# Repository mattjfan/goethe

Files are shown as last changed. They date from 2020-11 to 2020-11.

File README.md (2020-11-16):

# goethe
Accurate, low volume robotic color matching and mixing platform for medium to high viscosity paint

## What is this project?
The idea of this project is to create a physical version of the colorpicker/eyedropper or
palette creators you might see in a digital image-editing software like photoshop, but for paint
(and in theory other physical liquid mediums).

## What do we have so far?
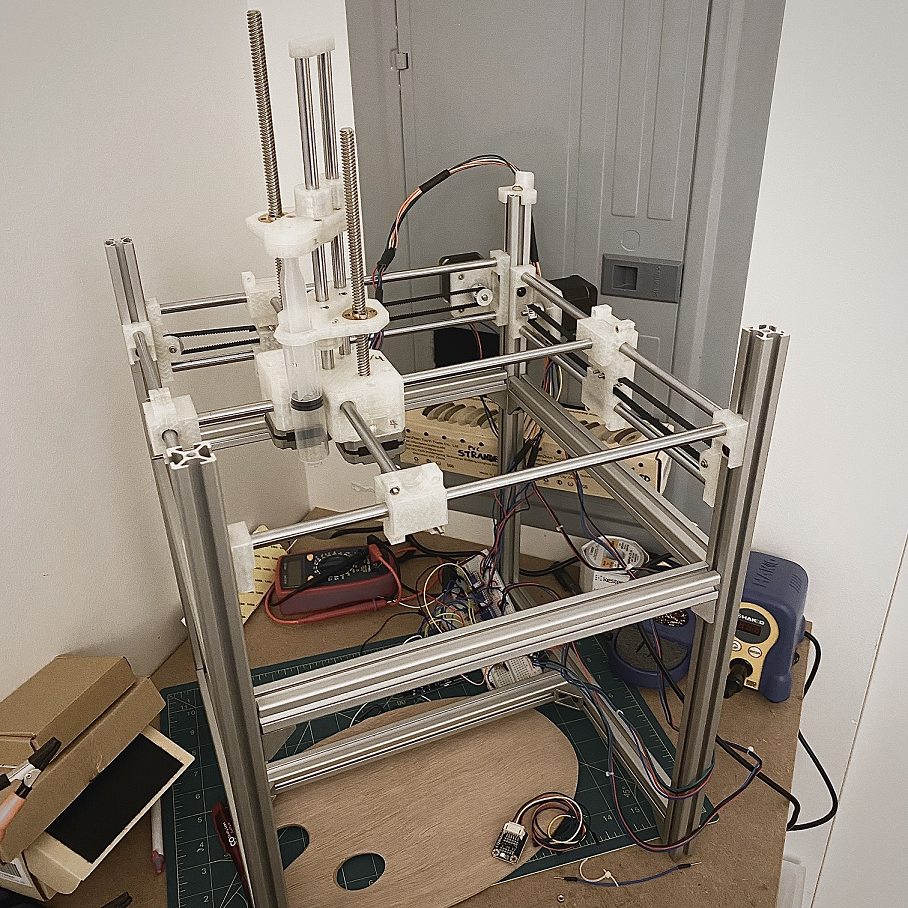
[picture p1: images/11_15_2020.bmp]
v1 prototype


A (grossly over-engineered, but still usable) prototype with XY-axis control, and a raisable and controllable syringe for picking up and putting down paints (and potentially stirring). Currently based on the Arduino UNO, will be moving to Arduino Mega soon for development, and considering out other AVR platforms for longer term after initial prototyping. The prototype has everything it needs for movement and controls, and has basic movement (non-control looped) for the carriage and the syringe already validated. Currently missing a platform to hold the paint and water reservoirs, and a sliding platform to hold the user's palette. Also not wired up for the color sensor yet, and I haven't made the CAD designs for the sensor pen/eyedropper (key thing here is that we want the tool to reject ambient light for color consistency across usage environments). A lot of the control code is written (but unvalidated), and is also pretty rough but usable. Actual wrappers for using the system for color mixing is still WIP.

*Important note: The repo right now is still just being used as a place for me to dump and track things as I continue development. As such, files may be disorganized or incorrectly labeled, code can be expected to still be buggy or unvalidated, and this repo may not contain all resources associated with the project, such as notes or a BOM for the non-3d-printed parts. You're free to try to build your own, but **be advised that some parts may be missing or unfinished**. If the results of this project turn out good, I'll go back through and do some housekeeping/updates later to make it easier to build your own.*

## Next Steps
Well, first I want to finish this prototype. Then, I want to mock a prototype that uses peristaltic pumps and a strain guage/scale as a 
potentially faster, cheaper, simpler design, and compare color accuracy and precision across the two designs. (This design was actually one of
the original concepts, although I rejected it bc I liked the elegance of the V1 design (only one extruder), and thought it may have issues with
accuracy. After seeing industrial paint mixing machines and that they work with a similar pump design, I figured it's worth revisiting (although it's
possible that the color accuracy of this design at low volume in contrast to paint can volume is just not very good). This design technically uses
more motors (and potentially even more if we want to add powered XY axis support for comparable workspace instead of static nozzle placement),
but the mixing process steps are likely simpler in this approach, and worth considering given the relatively cheap cost of peristaltic pumps.

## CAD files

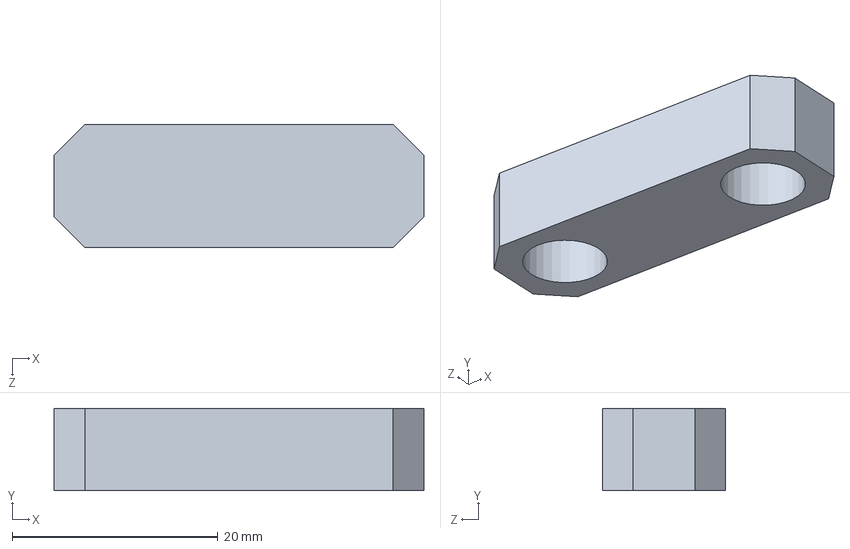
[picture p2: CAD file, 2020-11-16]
hardware/cad/dispenser/shaft_cap/shaft_cap_v1.SLDPRT
36.0 x 8.00 x 12.0 mm

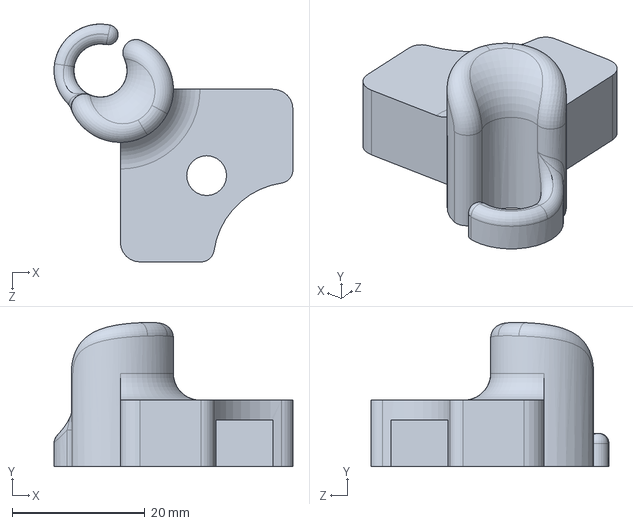
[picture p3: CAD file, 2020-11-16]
hardware/cad/extras/wire_guard/wire_guard.SLDPRT
36.0 x 21.7 x 35.8 mm

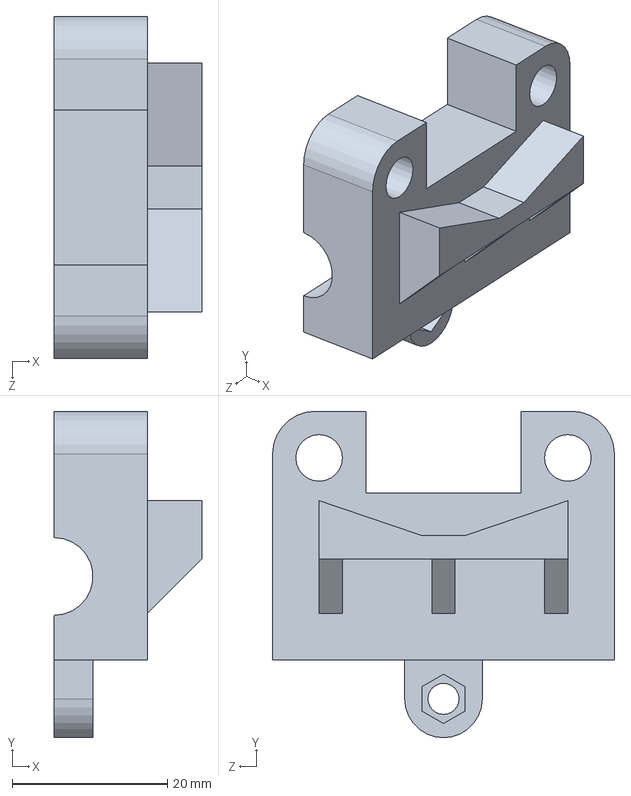
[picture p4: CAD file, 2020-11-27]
hardware/cad/gantry_v2/single_rod_slider_inside.SLDPRT
19.0 x 42.0 x 44.0 mm

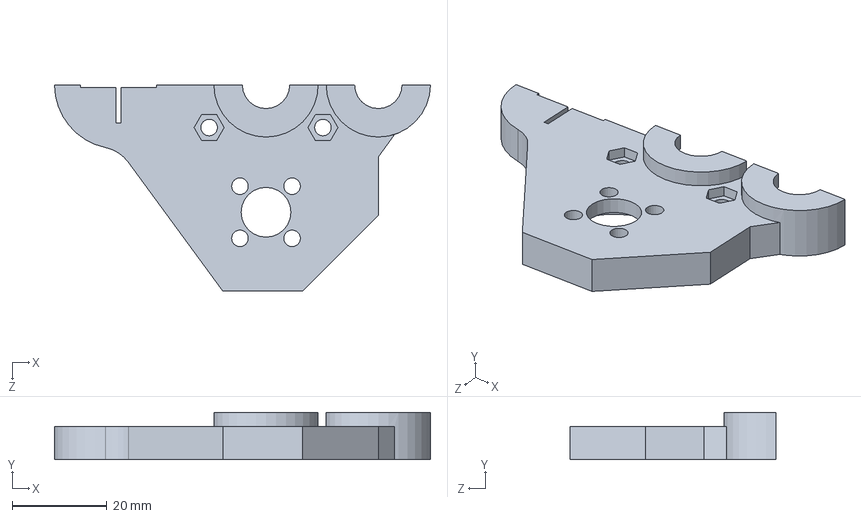
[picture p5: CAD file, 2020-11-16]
hardware/cad/plunger_plate/plunger_plate_hemi_L_v2.SLDPRT
79.3 x 10.0 x 43.5 mm

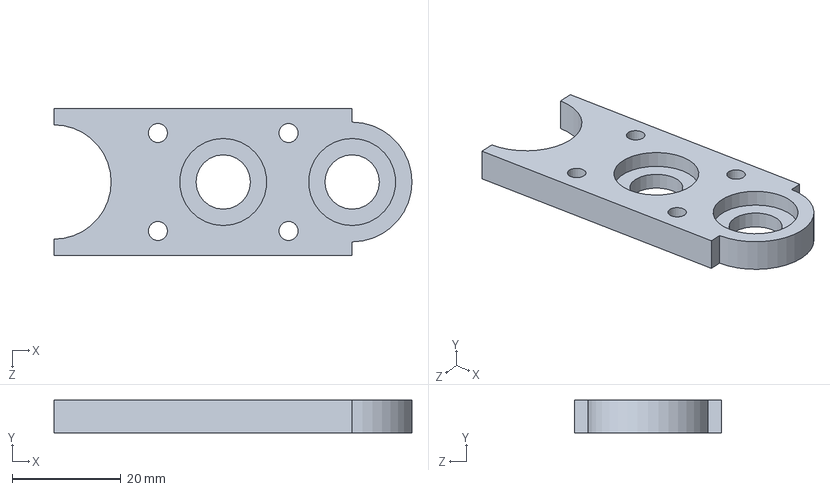
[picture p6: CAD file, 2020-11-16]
hardware/cad/syringe_plate/syringe_plate_cap_v1.SLDPRT
65.8 x 6.00 x 27.0 mm

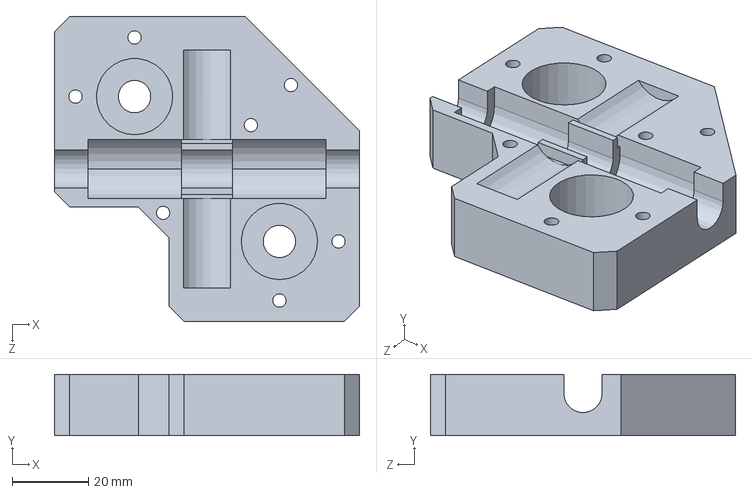
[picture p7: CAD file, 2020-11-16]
hardware/cad/dispenser/motor_plate/motor_plate_top_v4.SLDPRT
80.0 x 16.0 x 80.0 mm

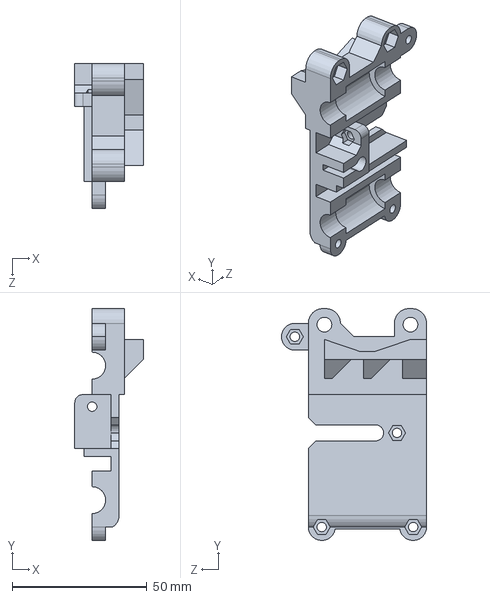
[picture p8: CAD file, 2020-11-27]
hardware/cad/gantry_v2/double_rod_slider_inside_v2.SLDPRT
25.5 x 86.2 x 54.0 mm

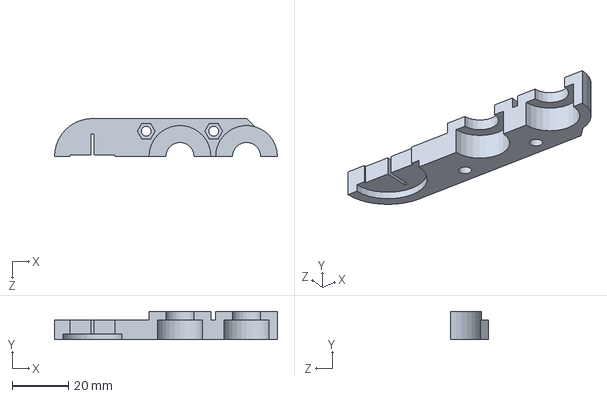
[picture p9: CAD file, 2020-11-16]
hardware/cad/plunger_plate/plunger_plate_hemi_S_v2.SLDPRT
79.3 x 10.0 x 13.5 mm

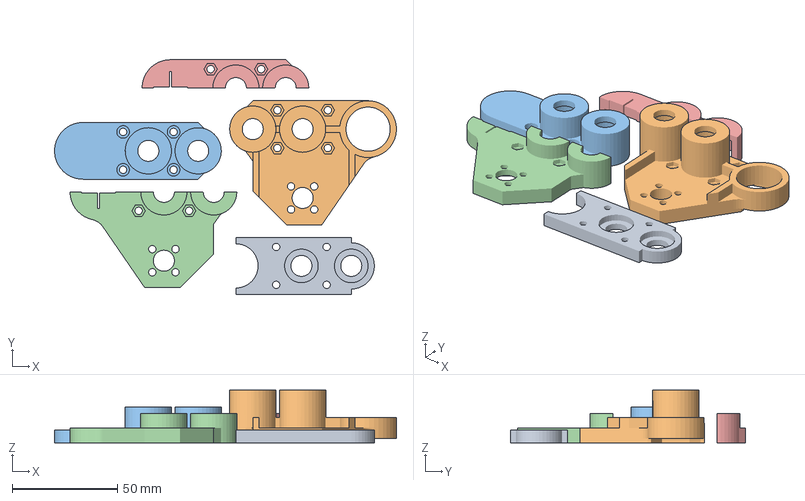
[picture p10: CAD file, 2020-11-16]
hardware/cad/syringe_plate/syringe_and_extruder_plates_v1.3mf
162.5 x 111.5 x 25.0 mm
syringe_plate_cap_v1.STL
syringe_plate_v1.STL
plunger_plate_cap_v1.STL
plunger_plate_hemi_L_v1.STL
plunger_plate_hemi_S_v1.STL

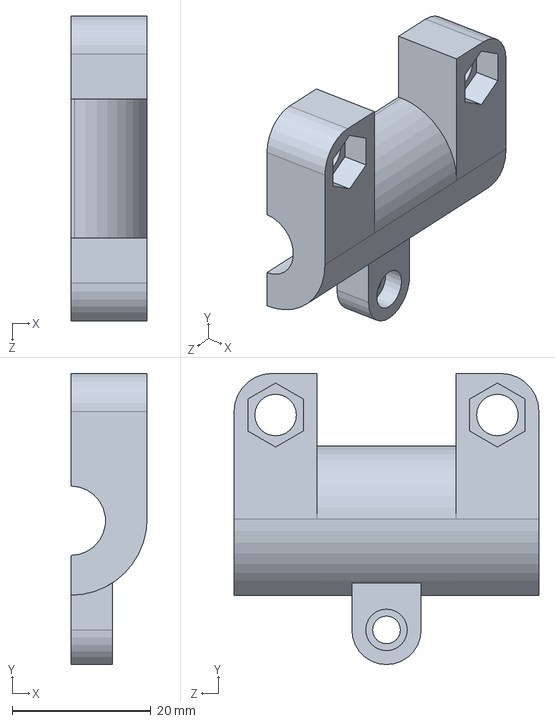
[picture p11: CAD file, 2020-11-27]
hardware/cad/gantry_v2/single_rod_slider_outside.SLDPRT
11.0 x 42.0 x 44.0 mm

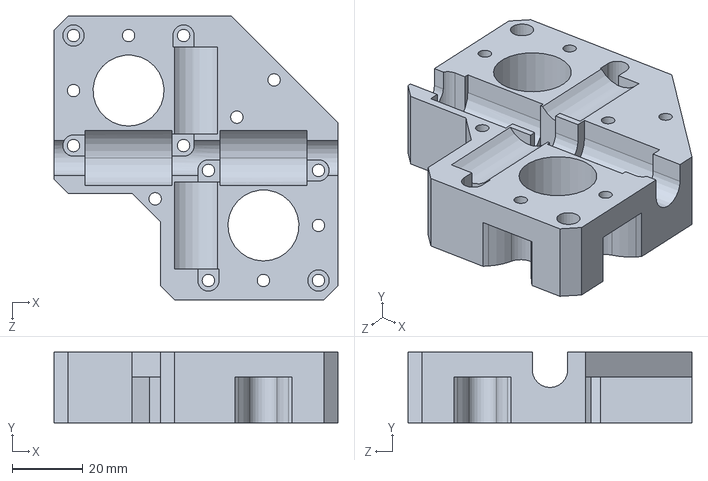
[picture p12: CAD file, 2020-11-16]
hardware/cad/dispenser/motor_plate/motor_plate_v4.SLDPRT
80.0 x 20.0 x 80.0 mm

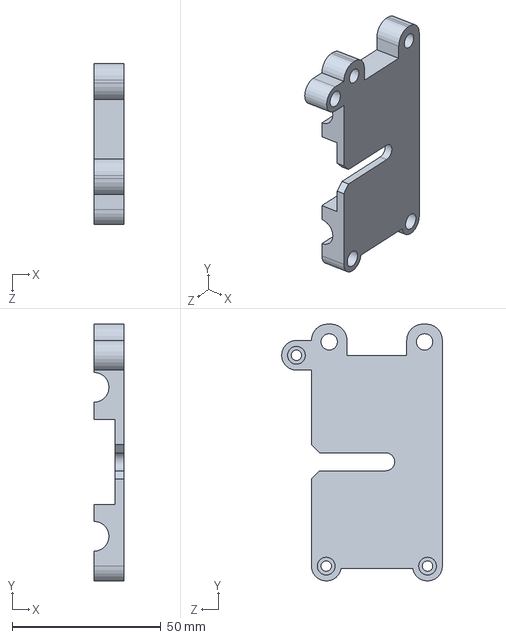
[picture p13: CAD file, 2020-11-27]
hardware/cad/gantry_v2/double_rod_slider_outside_v2.SLDPRT
10.0 x 86.2 x 54.0 mm

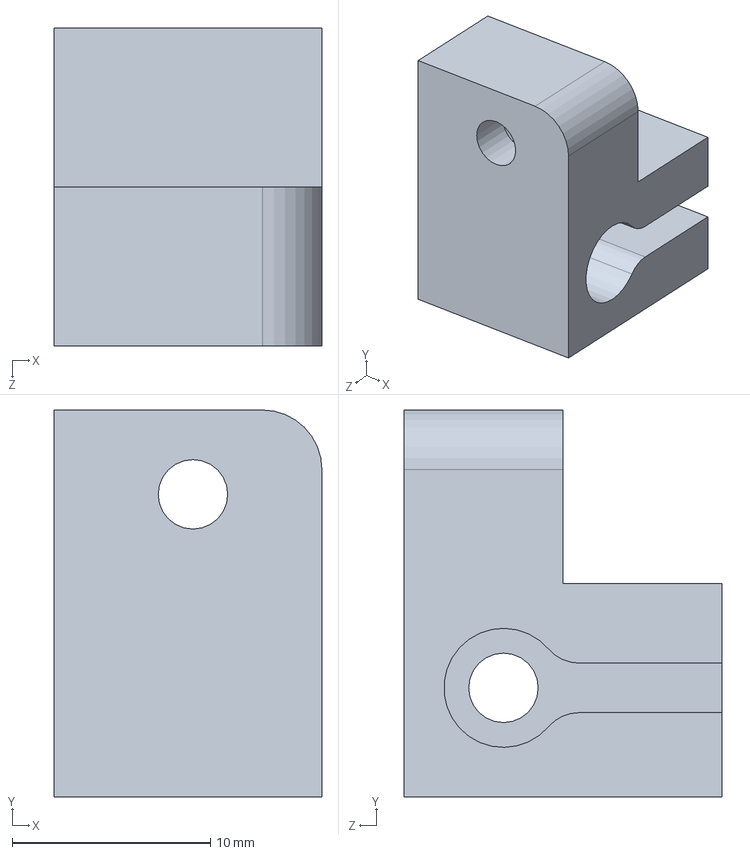
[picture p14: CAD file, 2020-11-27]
hardware/cad/gantry_v2/double_rod_slider_tensioner_v2.SLDPRT
13.5 x 19.5 x 16.0 mm

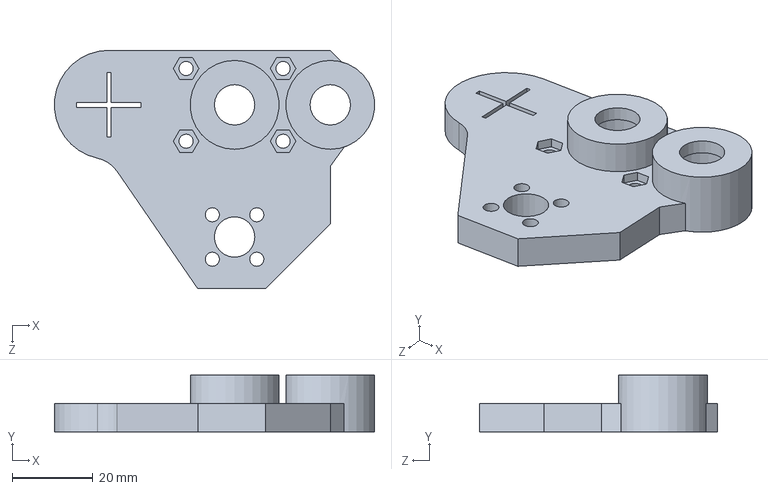
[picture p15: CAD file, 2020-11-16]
hardware/cad/plunger_plate/plunger_plate_v1.SLDPRT
79.2 x 14.0 x 59.0 mm

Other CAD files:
hardware/cad/syringe_plate/syringe_plate_v3.SLDPRT
hardware/cad/gantry_v2/single_rod_slider_outside_v2.SLDPRT
hardware/cad/gantry_v2/single_rod_slider_inside_v2.SLDPRT
hardware/cad/plunger_plate/plunger_plate_cap_v2.SLDPRT
hardware/cad/dispenser/motor_plate/motor_plate_top_v3.SLDPRT
hardware/cad/dispenser/motor_plate/motor_plate_top_v3.STL
hardware/cad/dispenser/motor_plate/motor_plate_top_v4.STL
hardware/cad/dispenser/motor_plate/motor_plate_v1.SLDPRT
hardware/cad/dispenser/motor_plate/motor_plate_v2.SLDPRT
hardware/cad/dispenser/motor_plate/motor_plate_v3.SLDPRT
hardware/cad/dispenser/motor_plate/motor_plate_v3.STL
hardware/cad/dispenser/motor_plate/motor_plate_v4.STL
hardware/cad/dispenser/shaft_cap/shaft_cap_v1.STL
hardware/cad/extras/wire_guard/wire_guard.STL
hardware/cad/gantry/double_rod_holder/double_rod_holder_v1.STL
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

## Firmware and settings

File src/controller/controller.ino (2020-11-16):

//#include "controller.h"
#include <EEPROM.h>
#include <TMCStepper.h>

#define LOC_RED (Point) {7, 13}
#define LOC_BLUE (Point) {0,0}
#define LOC_YELLOW (Point) {0,0}
#define LOC_BLACK (Point) {0,0}
#define LOC_WHITE (Point) {0,0}
#define LOC_DILUTE (Point) {0,0}
#define LOC_CLEAN (Point) {0,0}
#define HEIGHT_CALIBRATE 0 // Height for stall calibration, and lowest possible height. Should generally be 0
#define HEIGHT_LOAD HEIGHT_CALIBRATE
#define HEIGHT_MOVE 10 // Height for moving around. Should be tall enough to clear all obstacles, prob. want this to be your largest height
#define PLUNGER_MAX_HEIGHT 100 // Max height of plunger.
#define PLUNGER_DIAMETER 20
#define HEIGHT_DISPENSE HEIGHT_MOVE
#define HEIGHT_DISPENSE_WATER HEIGHT_DISPENSE // if you want to specify a water dispense height to minimize splashing
#define BB_DISPENSE_L (Point) {50,50} // closest to origin corner for dispensing bounding box
#define BB_DISPENSE_U (Point) (100,100} // farthest from origin corner for dispensing bounding box
#define CW HIGH
#define CCW LOW

#define STEPS_PER_REV (double) 200
#define MICROSTEPS (double) 8
#define DRIVE_PULLEY_RADIUS (double) 6.1 // in mm
#define DRIVE_SCREW_PITCH (double) 8.0 // in mm

#define STEP_DIST_SYRINGE ( DRIVE_SCREW_PITCH / ( STEPS_PER_REV * MICROSTEPS ))
#define STEP_DIST_X ( (2 * PI * DRIVE_PULLEY_RADIUS) / ( STEPS_PER_REV * MICROSTEPS ))
#define STEP_DIST_Y STEP_DIST_X

#define STALL_PIN_SYRINGE A0
#define STALL_PIN_PLUNGER A1
#define STALL_PIN_X A2
#define STALL_PIN_Y A3

#define MOTOR_SYRINGE StepperMotor(4, 5, STALL_PIN_SYRINGE, 3, STEP_DIST_SYRINGE, 140, CW) // defining motor wholesale as macro instead of individual pins
#define MOTOR_PLUNGER StepperMotor(6, 7, STALL_PIN_PLUNGER, 3, STEP_DIST_SYRINGE, 90, CW)
#define MOTOR_X StepperMotor(8, 9, STALL_PIN_X, A4, STEP_DIST_X, 280, CW)
#define MOTOR_Y StepperMotor(10, 11, STALL_PIN_Y, A5, STEP_DIST_Y, 280, CCW)

#define CONFIG_RX 12
#define CONFIG_TX 13
#define STALL_VALUE 40
#define DRIVER_ADDRESS 0b00 // TMC2209 Driver address according to MS1 and MS2

#define R_SENSE 0.11f // Match to your driver
                      // SilentStepStick series use 0.11
                      // UltiMachine Einsy and Archim2 boards use 0.2
                      // Panucatt BSD2660 uses 0.1
                      // Watterott TMC5160 uses 0.075

TMC2209Stepper driver(CONFIG_RX, CONFIG_TX, R_SENSE, DRIVER_ADDRESS);

using namespace TMC2208_n;

class StepperMotor {
  public:
//    StepperMotor(int step_pin, int dir_pin, int stall_pin = -1, int enable_pin = -1, double mm_per_step = 0, int step_delay = 1) {
//      this->step_pin = step_pin;
//      this->dir_pin = dir_pin;
//      this->stall_pin = stall_pin;
//      this->enable_pin = enable_pin;
//      this->step_delay = step_delay;
//      this->mm_per_step = mm_per_step;
//      pinMode(step_pin, OUTPUT);
//      pinMode(dir_pin, OUTPUT);
//      if (stall_pin >= 0) {
//        this->stall_pin = stall_pin;
//        pinMode(stall_pin, INPUT);
//      }
//      if (enable_pin >= 0) {
//        this->enable_pin = enable_pin;
//        pinMode(enable_pin, OUTPUT);
//        digitalWrite(enable_pin, LOW);
//      }
//    }
//    StepperMotor( int step_pin, int dir_pin, double mm_per_step, int step_delay = 1) {
//    }
//    StepperMotor( int step_pin, int dir_pin, int stall_pin, double mm_per_step, int step_delay = 1) {
//     
//    }
    StepperMotor( int step_pin, int dir_pin, int stall_pin, int enable_pin, double mm_per_step, double max_pos, double increasing_direction = CW, int step_delay = 1) {
      this->step_pin = step_pin;
      this->dir_pin = dir_pin;
      this->stall_pin = stall_pin;
      this->enable_pin = enable_pin;
      this->mm_per_step = mm_per_step;
      this->step_delay = step_delay;
      this->max_pos = max_pos;
      this->inc_dir = increasing_direction;
      pinMode(step_pin, OUTPUT);
      pinMode(dir_pin, OUTPUT);
      pinMode(stall_pin, INPUT); // included with next gen design in mind. Currently not used internally, stall refs currently managed in global scope
      pinMode(enable_pin, INPUT);
    }
    void step_dist_cw(double dist, int step_delay = 1) {
      step_cw((int) dist / mm_per_step, step_delay);
    }
    void go_up(double dist) {
      double target_pos = pos + dist;
      if (target_pos > max_pos) {
        target_pos = max_pos;
      }
      digitalWrite(step_pin, LOW);
      digitalWrite(dir_pin, inc_dir);
      while (pos < target_pos) {
        digitalWrite(step_pin, HIGH);
        delayMicroseconds(step_delay);
        digitalWrite(step_pin, LOW);
        pos += mm_per_step;
      }
    }

    void go_down(double dist) {
      double target_pos = pos - dist;
      if (target_pos < 0) {
        target_pos = 0;
      }
      digitalWrite(step_pin, LOW);
      digitalWrite(dir_pin, !inc_dir);
      while (pos > target_pos) {
        digitalWrite(step_pin, HIGH);
        delayMicroseconds(step_delay);
        digitalWrite(step_pin, LOW);
        pos -= mm_per_step;
      }
    }

    void go_to_position(double target_position) {
//      Serial.println("Goin to tha position");
      if (target_position > max_pos) {
        return;
      }
      digitalWrite(step_pin, LOW);
      if (pos < target_position) {
        digitalWrite(dir_pin, inc_dir);
        while (pos < target_position) {
          digitalWrite(step_pin, HIGH);
          delayMicroseconds(step_delay);
          digitalWrite(step_pin, LOW);
          pos += mm_per_step;
        }
      } else if (pos > target_position) {
        digitalWrite(dir_pin, !inc_dir);
        while (pos > target_position) {
          digitalWrite(step_pin, HIGH);
          delayMicroseconds(step_delay);
          digitalWrite(step_pin, LOW);
          pos -= mm_per_step;
        }
      } 
    }
    void step_cw(int num_steps, int step_delay = 1) {
      step_(num_steps, CW, step_delay);
    }

    void step_ccw(int num_steps, int step_delay = 1) {
      step_(num_steps, CCW, step_delay);
    }

    void step(int dir, int delay_micros = 20) {
      digitalWrite(dir_pin, dir);
      digitalWrite(step_pin, HIGH);
      delayMicroseconds(delay_micros);
      digitalWrite(step_pin, LOW);
    }
    void calibrate() {
      digitalWrite(dir_pin, !inc_dir);
      digitalWrite(step_pin, LOW);
//      while(1) {
      for (int i = 0; i <= round(max_pos / mm_per_step); i++) { // times out if stall isn't triggered 
        if (isStalled()) {
          break;
        }
        digitalWrite(step_pin, HIGH);
        delay(step_delay);
        digitalWrite(step_pin, LOW);
      }
      pos = 0;
    }
    void calibrate_reverse() { // calibrate to max_pos instead of zero
      digitalWrite(dir_pin, inc_dir);
      digitalWrite(step_pin, LOW);
      for (int i = 0; i <= round(max_pos / mm_per_step); i++) { // times out if stall isn't triggered 
        if (isStalled()) {
          break;
        }
        digitalWrite(step_pin, HIGH);
        delay(step_delay);
        digitalWrite(step_pin, LOW);
      }
      pos = max_pos;
    }
//    void calibrate(int dir, int step_delay = -1) { // TODO: may want to add a max timeout option
//      digitalWrite(dir_pin, dir);
//      if (step_delay < 0) {
//        step_delay = this->step_delay;
//      }
//      while(1) {
//        if (isStalled()) {
//          break;
//        }
//        digitalWrite(step_pin, HIGH);
//        delay(step_delay);
//        digitalWrite(step_pin, LOW);
//      }
//      // clean-up so motor can be used again.
//      reset();
//    }
    void setStalled(bool isStalled) { // kludge so that global interrupt handlers can set this value
      stalled = isStalled;
    }
    bool isStalled() {
      return stalled;
//      if (stall_pin >= 0 &&
//        digitalRead(stall_pin) == HIGH) {
//         Serial.println("Fuck, we stalled");
//        return true;
//      }
//      return false;
    }

    void reset() {
      this->disable();
      delay(this->reset_delay);
      this->enable();
      this->stalled = false;
    }

    void enable() {
      digitalWrite(enable_pin, LOW);
    }
    
    void disable() {
      digitalWrite(enable_pin, HIGH);
    }
    
  private:
    int step_pin;
    int dir_pin;
    int stall_pin;
    int enable_pin;
    int step_delay;
    double mm_per_step;
    int inc_dir = CW;
    double pos = 0;
    double max_pos;
    int reset_delay = 20;
    bool stalled = false;
    void interrupt_handler () {
      stalled = true;
    }
    void step_(int num_steps, int dir, int step_delay = -1) {
      if (step_delay < 0) {
        step_delay = this->step_delay; // reset local reference
        // I think this is mem safe bc step_delay should be passed by value
      }
      digitalWrite(dir_pin, dir);
      for (int i = 0; i < num_steps; i++) {
        digitalWrite(step_pin, HIGH);
        delay(step_delay);
//        delayMicroseconds(100);
        digitalWrite(step_pin, LOW);
        if (isStalled()) {
          reset();
          break;
        }
      }
    }
};

//class GantryAxis {
//  public:
//    GantryAxis(StepperMotor motor) {
//    }
//}

class Syringe {
  public:
    Syringe(StepperMotor body, StepperMotor plunger, double diameter = 10.0, double step_distance = 0.1, int step_delay = 1){
      *(this->body_ptr) = body;
      *(this->plunger_ptr) = plunger;
      this->step_distance = step_distance;
      this->UP_DIR = CW;
      this->diameter = diameter;
      this->step_distance = step_distance;
      this->step_delay = step_delay;
    }
    void moveTo(float target_height){ // TODO: check that it moves within height bounds
      if (target_height > syringe_height) {
        while(target_height > syringe_height) {
          body.step(UP_DIR); // technically not truly synchronous...
          plunger.step(UP_DIR);
          delay(step_delay);
          syringe_height += step_distance;
        }
      } else {
        while(target_height < syringe_height) {
          body.step(!UP_DIR);
          plunger.step(!UP_DIR);
          delay(step_delay);
          syringe_height -= step_distance;
        }
      }
    }
    void load(double volume) { // volume in mm^3
      double target_height = plunger_height + heightFromVolume(volume); // v = PI * d^2 * h / 4
      while(plunger_height < target_height){
        plunger.step(UP_DIR);
        delay(step_delay);
        plunger_height += step_distance;
      }
    }
    void dispense(double volume) {
      double target_height = plunger_height - heightFromVolume(volume);
      while (plunger_height > target_height) {
        plunger.step(!UP_DIR);
        delay(step_delay);
        plunger_height -= step_distance;
      }
    }
  private:
    double heightFromVolume(double volume) {
      return (4.0 * volume) / (PI * diameter * diameter);
    }
    StepperMotor &body = *body_ptr; // kludge to reference by name
                              // should probably refactor at some point to
                              // declare with .h/.hpp and use an initializer list
    StepperMotor &plunger = *plunger_ptr;
    
    
    StepperMotor* body_ptr = nullptr;
    StepperMotor* plunger_ptr = nullptr;
    int UP_DIR;
    double syringe_height = 0.0;
    double plunger_height = 0.0;
    double step_distance;
    double diameter;
    int step_delay;
};

class Gantry {
  public:
    Gantry(double step_distance = 0.1){
      
    }
  private:
    double x, y;
};

typedef struct Point {
  int x;
  int y;
} Point;

class Color {
  public:
    Color(double r, double b, double y, double w, double k) {
      // basic color w/ no water dilution
      double sum = r + b + y + w + k;
      this->r_ = r /= sum;
      this->b_ = b /= sum;
      this->y_ = y /= sum;
      this->w_ = w /= sum;
      this->k_ = k /= sum;
      this->c_ = 0.0;
    }
    
    Color(double r, double b, double y, double w, double k, double c) {
      // allow for specifying water % for diluted / wet mixes
      double sum = r + b + y + w + k + c;
      this->r_ = r /= sum;
      this->b_ = b /= sum;
      this->y_ = y /= sum;
      this->w_ = w /= sum;
      this->k_ = k /= sum;
      this->c_ = c /= sum;
    }
    
    const double &r = r_;
    const double &b = b_;
    const double &y = y_;
    const double &w = w_;
    const double &k = k_;
    const double &c = c_;
  private:
    double r_;
    double b_;
    double y_;
    double w_;
    double k_;
    double c_;
};

void configure_stallguard() {
  driver.beginSerial(19200);
  driver.begin();
  driver.toff(4);
  driver.blank_time(24);
  driver.rms_current(400); // mA
  driver.microsteps(MICROSTEPS); // was originally set at 16
  driver.TCOOLTHRS(0xFFFFF); // 20bit max
  driver.semin(5);
  driver.semax(2);
  driver.sedn(0b01);
  driver.SGTHRS(STALL_VALUE);
}
/**
 * Basic motor tests checking for movement
 */
void motor_test_basic(int steps = 1500, int period = 3){
  // testing syringe motor
  if(Serial) {
    Serial.print("Testing syringe...");
  }
  MOTOR_SYRINGE.reset();
  MOTOR_SYRINGE.step_cw(steps, period);
  MOTOR_SYRINGE.step_ccw(steps, period);
  if (Serial) {
    Serial.println("done.");
  }
  // testing plunger motor
  if(Serial) {
    Serial.print("Testing plunger...");
  }
  MOTOR_PLUNGER.reset();
  MOTOR_PLUNGER.step_cw(steps, period);
  MOTOR_PLUNGER.step_ccw(steps, period);
  if (Serial) {
    Serial.println("done.");
  }
  // testing x carriage motor
  if(Serial) {
    Serial.print("Testing X carriage...");
  }
  MOTOR_X.reset();
  MOTOR_X.step_cw(steps, period);
  MOTOR_X.step_ccw(steps, period);
  if (Serial) {
    Serial.println("done.");
  }
  // testing y carriage motor
  if(Serial) {
    Serial.print("Testing Y carriage...");
  }
  MOTOR_Y.reset();
  MOTOR_Y.step_cw(steps, period);
  MOTOR_Y.step_ccw(steps, period);
  if (Serial) {
    Serial.println("done.");
  }
}

// callback for computer serial command interface
bool queue_events = false; // should events be queued
bool serial_blocked = false; // global flag to let us know if we should throw stuff away
void serialEvent() {
  String s = Serial.readStringUntil('\n');
  if (serial_blocked && !queue_events) { // throw away events received while you were running old event
    // unless you have queueing of events turned on.
    Serial.println("Ignoring message " + s); // Say that event is being thrown away
  } else { // main logic block goes here
      serial_blocked = true;
      serialCallback(s);
  }
  if (!Serial.available()) { // Unblocking new events if we've processed all stale events
      serial_blocked = false;
  }
}

void serialCallback(String msg) {
  String command = "";
  String payload = "";
  int argc = 1;
  String str = "";
  bool isCommand = true;
  for (char const &c: msg) {
    if (isCommand) {    
      if (c != ' ') {
        command += c;
      } else {
        isCommand = false;
      }
    } else {
      payload += c;
    }
  }
  if (command == "calibrate") {
    if (payload == "x") {
      Serial.print("Calibrating X-axis...");
      MOTOR_X.calibrate();
      Serial.println("done.");
    } else {
      Serial.println("Unrecognized argument " + payload + " for command " + command);
    }
  } else if (command == "movex") {
    double pos = payload.toDouble();
    if (pos || payload == "0" || payload == "0.0") {
      Serial.println(pos);
      MOTOR_X.go_to_position(pos);
      Serial.println("At requested position");
      
    } else {
      Serial.println("Unrecognized argument " + payload + " for command " + command);
    }
  } else {
    Serial.println("Unrecognized command " + command);
  }

//  if (msg == "calibrate x") {
//    // do calibration
//  } else if ( msg
//      Serial.println("Hello " + msg);
//      delay(5000);
//      Serial.println("Goodbye " + msg);
}

void syringe_interrupt_handler() {
  MOTOR_SYRINGE.setStalled(true);
}

void plunger_interrupt_handler() {
  MOTOR_PLUNGER.setStalled(true);
}

void x_interrupt_handler() {
  MOTOR_X.setStalled(true);
}

void y_interrupt_handler() {
  MOTOR_Y.setStalled(true);
}



void setup() {
  // put your setup code here, to run once:
  configure_stallguard();
  Serial.begin(9600);
  while(!Serial){}
  Serial.println("Starting");
  // Below is kludge to hook up motor stall pins to interrupts
  // ideally this could be handled in the class directly, but the instance method prototypes can't be used directly with attachInterrupt
  // and I can't use non-standard C++ libraries in AVR w/o adding extra bulk
  // Could theoretically also do live polling in the main loop, but would then have to wrangle all of our tasks into short-lived enough to be viable
  // in that approach... 
  // This current approach is messy, and strews the innards of our motor abstraction all over the place (and also exposes internal state for stall setting)
  // but it *should* at least work for now without needing to add extra stuff to AVR deps
  // May revisit this later, and end up adding the extra dependencies for a less fubar approach
  pinMode(STALL_PIN_SYRINGE, INPUT);
  pinMode(STALL_PIN_PLUNGER, INPUT);
  pinMode(STALL_PIN_X, INPUT);
  pinMode(STALL_PIN_Y, INPUT);
  attachInterrupt(digitalPinToInterrupt(STALL_PIN_SYRINGE), syringe_interrupt_handler, RISING);
  attachInterrupt(digitalPinToInterrupt(STALL_PIN_PLUNGER), plunger_interrupt_handler, RISING);
  attachInterrupt(digitalPinToInterrupt(STALL_PIN_X), x_interrupt_handler, RISING);
  attachInterrupt(digitalPinToInterrupt(STALL_PIN_Y), y_interrupt_handler, RISING);
//  readStringUntil(
//  configure_stallguard();
//  motor_test_basic(2400,1);
//  Serial.println("Finishing");
  
//  Serial.begin(9600);
//  Serial.print("What up hello!\n");
//  Serial.print("Red x: ");
//  Serial.print(LOC_RED.x);
//  Serial.print(", y: ");
//  Serial.print(LOC_RED.y);
//  Serial.print("\n");
//  Serial.print("Dispensing height: ");
//  Serial.print(HEIGHT_DISPENSE);
//  delay(2000);
//  Serial.println("");
//  Serial.println("Starting: ");
//  MOTOR_SYRINGE.reset();
//  MOTOR_SYRINGE.step_cw(5000, 1);
//  MOTOR_SYRINGE.step_ccw(2400, 1);
//  Serial.print("steps done");

}

void calibrate_xy() {

}

void calibrate_needle() {
  // may want to run calibrate_xy before this.
//  go_to(LOC_CLEAN);  
}

void go_to(Point pt) {
  return;
}

void make_color(Point pt, Color color) {
}

void set_height() {
  
}

void calibrate() {
// go_to(
}

void loop() {
  // put your main code here, to run repeatedly:
 

}

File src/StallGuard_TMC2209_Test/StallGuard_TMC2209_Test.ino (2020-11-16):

/**
 * Author Teemu Mäntykallio
 *
 * Plot TMC2130 or TMC2660 motor load using the stallGuard value.
 * You can finetune the reading by changing the STALL_VALUE.
 * This will let you control at which load the value will read 0
 * and the stall flag will be triggered. This will also set pin DIAG1 high.
 * A higher STALL_VALUE will make the reading less sensitive and
 * a lower STALL_VALUE will make it more sensitive.
 *
 * You can control the rotation speed with
 * 0 Stop
 * 1 Resume
 * + Speed up
 * - Slow down
 */
#include <TMCStepper.h>
#include <SoftwareSerial.h>

#define MAX_SPEED        40 // In timer value
#define MIN_SPEED      1000

#define STALL_VALUE     30// [0..255]

#define EN_PIN           13 // Enable
#define DIR_PIN          11 // Direction
#define STEP_PIN         10 // Step
#define SW_RX            8 // TMC2208/TMC2224 SoftwareSerial receive pin
#define SW_TX            9 // TMC2208/TMC2224 SoftwareSerial transmit pin
//#define SERIAL_PORT Serial1 // TMC2208/TMC2224 HardwareSerial port
#define SERIAL_PORT SoftwareSerial(SW_RX, SW_TX)
#define DRIVER_ADDRESS 0b00 // TMC2209 Driver address according to MS1 and MS2

#define R_SENSE 0.11f // Match to your driver
                      // SilentStepStick series use 0.11
                      // UltiMachine Einsy and Archim2 boards use 0.2
                      // Panucatt BSD2660 uses 0.1
                      // Watterott TMC5160 uses 0.075

// Select your stepper driver type
//TMC2209Stepper driver(&SERIAL_PORT, R_SENSE, DRIVER_ADDRESS);
TMC2209Stepper driver(SW_RX, SW_TX, R_SENSE, DRIVER_ADDRESS);

using namespace TMC2208_n;

// Using direct register manipulation can reach faster stepping times
#define STEP_PORT     PORTF // Match with STEP_PIN
#define STEP_BIT_POS      0 // Match with STEP_PIN

ISR(TIMER1_COMPA_vect){
  //STEP_PORT ^= 1 << STEP_BIT_POS;
  digitalWrite(STEP_PIN, !digitalRead(STEP_PIN));
}

void setup() {
  Serial.begin(250000);         // Init serial port and set baudrate
  while(!Serial);               // Wait for serial port to connect
  Serial.println("\nStart...");

//  SERIAL_PORT.begin(115200);
  driver.beginSerial(19200);
//  driver.beginSerial(115200);

  pinMode(EN_PIN, OUTPUT);
  pinMode(STEP_PIN, OUTPUT);
  pinMode(DIR_PIN, OUTPUT);
  digitalWrite(EN_PIN, LOW);

  driver.begin();
  driver.toff(4);
  driver.blank_time(24);
  driver.rms_current(400); // mA
  driver.microsteps(16);
  driver.TCOOLTHRS(0xFFFFF); // 20bit max
  driver.semin(5);
  driver.semax(2);
  driver.sedn(0b01);
  driver.SGTHRS(STALL_VALUE);

  // Set stepper interrupt
  {
    cli();//stop interrupts
    TCCR1A = 0;// set entire TCCR1A register to 0
    TCCR1B = 0;// same for TCCR1B
    TCNT1  = 0;//initialize counter value to 0
    OCR1A = 256;// = (16*10^6) / (1*1024) - 1 (must be <65536)
    // turn on CTC mode
    TCCR1B |= (1 << WGM12);
    // Set CS11 bits for 8 prescaler
    TCCR1B |= (1 << CS11);// | (1 << CS10);
    // enable timer compare interrupt
    TIMSK1 |= (1 << OCIE1A);
    sei();//allow interrupts
  }
}

void loop() {
  static uint32_t last_time=0;
  uint32_t ms = millis();

  while(Serial.available() > 0) {
    int8_t read_byte = Serial.read();
    #ifdef USING_TMC2660
      if (read_byte == '0')      { TIMSK1 &= ~(1 << OCIE1A); driver.toff(0); }
      else if (read_byte == '1') { TIMSK1 |=  (1 << OCIE1A); driver.toff(driver.savedToff()); }
    #else
      if (read_byte == '0')      { TIMSK1 &= ~(1 << OCIE1A); digitalWrite( EN_PIN, HIGH ); }
      else if (read_byte == '1') { TIMSK1 |=  (1 << OCIE1A); digitalWrite( EN_PIN,  LOW ); }
    #endif
    else if (read_byte == '+') { if (OCR1A > MAX_SPEED) OCR1A -= 20; }
    else if (read_byte == '-') { if (OCR1A < MIN_SPEED) OCR1A += 20; }
  }

  if((ms-last_time) > 100) { //run every 0.1s
    last_time = ms;

    Serial.print("0 ");
    Serial.print(driver.SG_RESULT(), DEC);
    Serial.print(" ");
    Serial.println(driver.cs2rms(driver.cs_actual()), DEC);
  }
}

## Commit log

2020-11-16 initial public commit (still super rough, WIP)
    [double_rod_holder_v1.SLDPRT, double_rod_holder_v1.STL, double_rod_holder_v2.SLDPRT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]
2020-11-16 add board details
2020-11-27 starter files for pcb, add new gantry design
    [double_rod_slider_inside_v2.SLDPRT, double_rod_slider_inside_v2.STL, double_rod_slider_outside_v2.SLDPRT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]
